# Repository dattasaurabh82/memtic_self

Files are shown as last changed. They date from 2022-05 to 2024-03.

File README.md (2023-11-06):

# memtic_self

* [PROJECT PAGE](https://www.dattasaurabh.com/mi-e-metic-self)
* [INSTALLATION GUIDE](https://dattabaumstudio.notion.site/Mimetic-self-Installation-and-Maintenance-Guide-89d1f03d15b848089516b9a0ae4b9f4f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)

## System Architecture overview:
```mermaid
sequenceDiagram
    autonumber
    participant Processing_GUI
    participant python_AI_API_req_maker
    participant img_data.json
    participant python_gif_req_maker
    participant gif_data.json
    participant PI_python_OMX_player
    participant HW_swiper

    Note over Processing_GUI: mount network loaction of PI
    loop Every few minutes (configurable in app)
        Processing_GUI->>PI_python_OMX_player:  MQTT: stop omx player

        Note over Processing_GUI: capture image
        
        alt got captions and bounding box
            Processing_GUI->>python_AI_API_req_maker: CMD: raw.png + img_data.json

            activate Processing_GUI

            python_AI_API_req_maker-->>img_data.json: FILE_IO: formatted json response
            
            img_data.json-->>Processing_GUI: FILE_IO:parse a random caption and bounding boxes
            
            Processing_GUI->>python_gif_req_maker: CMD: caption + gif_data.json

            activate python_gif_req_maker

            python_gif_req_maker-->>gif_data.json: FILE_IO: formatted json response

            gif_data.json-->>Processing_GUI: FILE_IO: parse gif url

            deactivate python_gif_req_maker

            Note over Processing_GUI: download gif in network location

            Processing_GUI->>PI_python_OMX_player: CURL: MQTT: start omx player 

            deactivate Processing_GUI

            Note over PI_python_OMX_player: loop new GIF
        
        else caption req error
            Processing_GUI-xpython_AI_API_req_maker: CMD: raw.png + img_data.json

            activate Processing_GUI
            
            python_AI_API_req_maker-ximg_data.json: FILE_IO: exception for json response
            
            Processing_GUI->>PI_python_OMX_player: CURL: show error gif + MQTT: start omx player 

            deactivate Processing_GUI

            Note over PI_python_OMX_player: loop error fixed GIF
        else gif req error
            Processing_GUI->>python_AI_API_req_maker: CMD: raw.png + img_data.json

            activate Processing_GUI
            
            python_AI_API_req_maker->>img_data.json: FILE_IO: exception for json response

            img_data.json-->>Processing_GUI: FILE_IO:parse a random caption and bounding boxes
            
            Processing_GUI-xpython_gif_req_maker: CMD: caption + gif_data.json

            python_gif_req_maker--xgif_data.json: FILE_IO: exception for json response

            Processing_GUI->>PI_python_OMX_player: CURL: show error gif + MQTT: start omx player 

            deactivate Processing_GUI

            Note over PI_python_OMX_player: loop error fixed GIF
        end

        Note over Processing_GUI,HW_swiper: In any case, it send a swipe signal and awaits for swipe finish

        Processing_GUI->>HW_swiper: SERIAL: scroll tiktok
        activate Processing_GUI
       
        Note over HW_swiper: Swipe
        
        activate HW_swiper
        
        HW_swiper->>Processing_GUI: done swipping
        deactivate HW_swiper
        deactivate Processing_GUI
    end
    
```

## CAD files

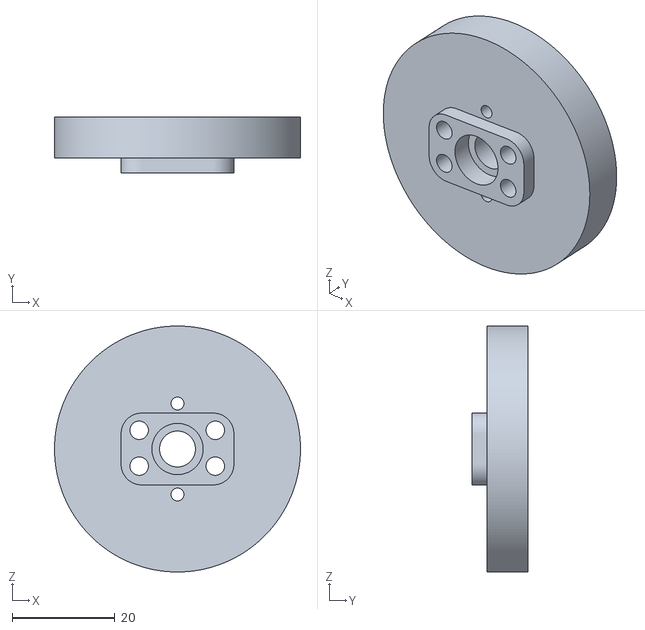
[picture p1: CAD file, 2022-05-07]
3D parts and laser cuts/camSwipper/CameraHolder.stl
48.0 x 11.0 x 48.0

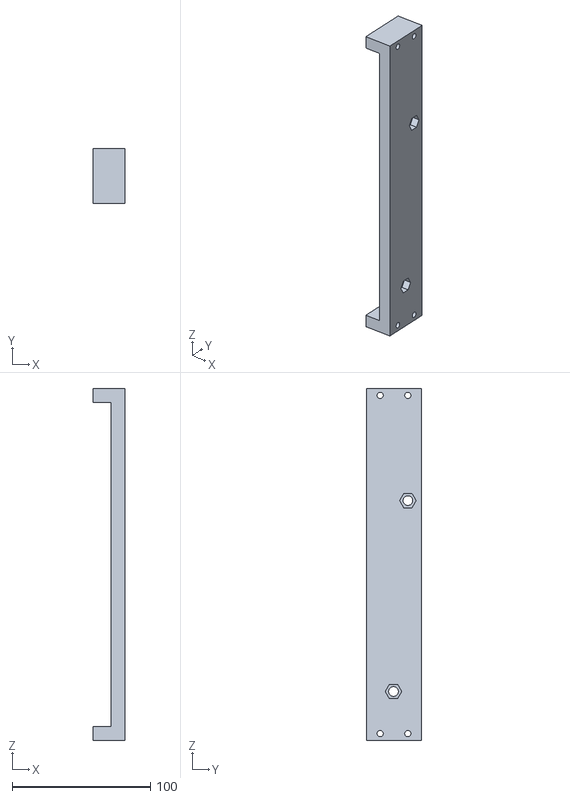
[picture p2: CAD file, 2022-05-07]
3D parts and laser cuts/ScreenHolder.stl
23.2 x 40.0 x 255.0

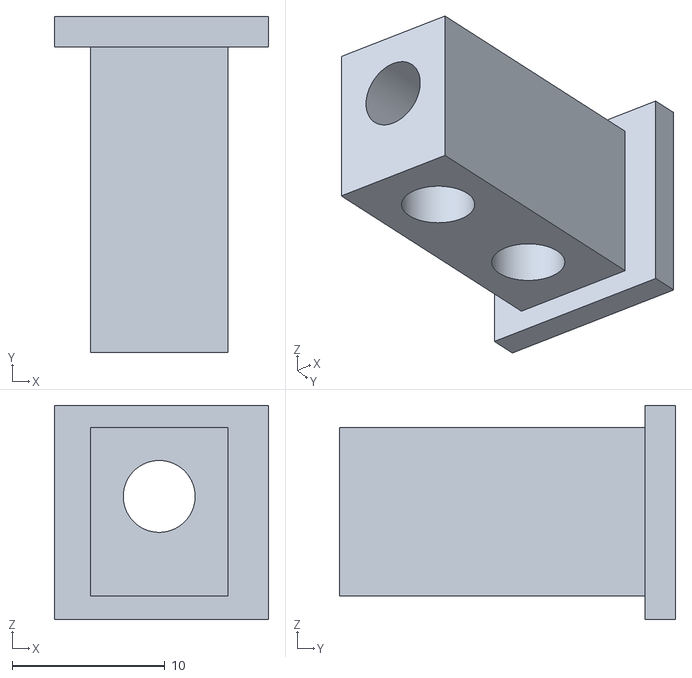
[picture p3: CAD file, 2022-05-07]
3D parts and laser cuts/camSwipper/HolderConnector.stl
14.0 x 22.0 x 14.0

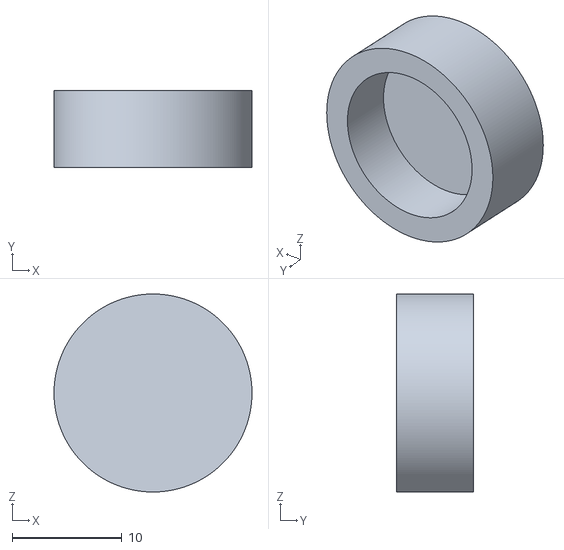
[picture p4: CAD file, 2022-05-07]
3D parts and laser cuts/bearingCover.stl
18.0 x 7.00 x 18.0

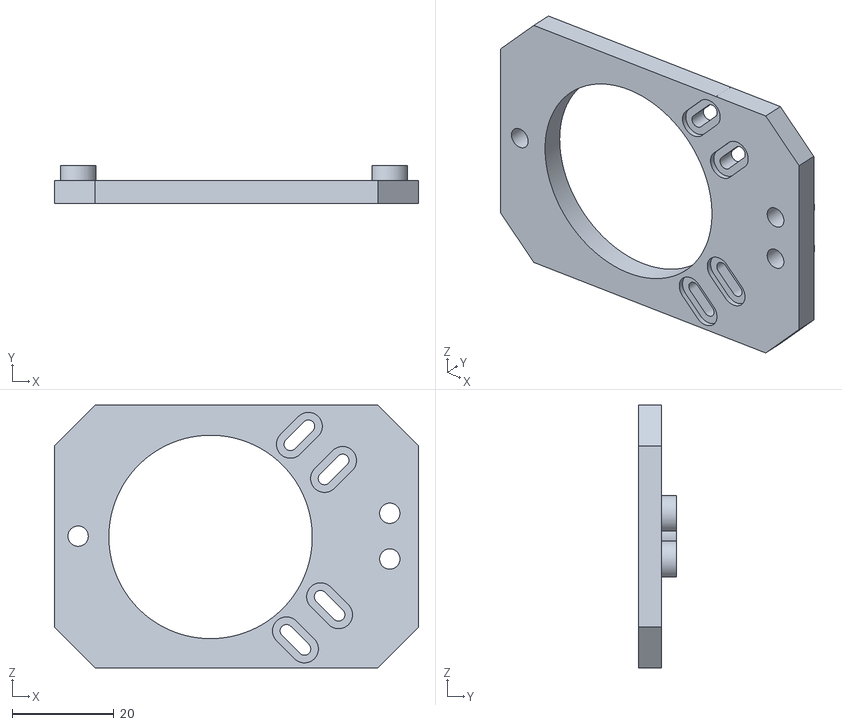
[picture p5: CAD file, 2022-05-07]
3D parts and laser cuts/camSwipper/TopPlateBigHole.stl
71.6 x 7.50 x 51.7

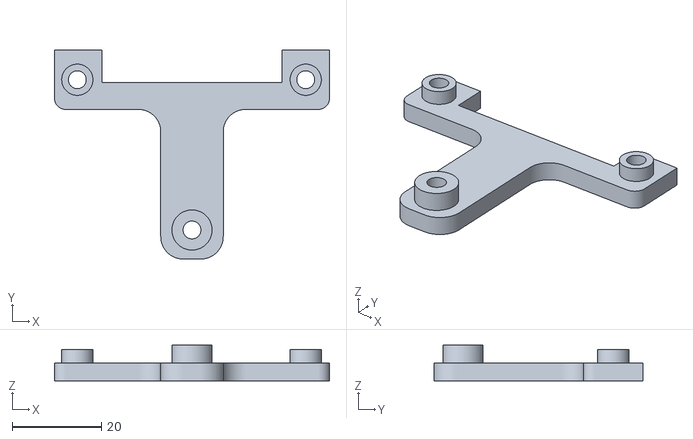
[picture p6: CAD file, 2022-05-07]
3D parts and laser cuts/camSwipper/FrontRightHolder.stl
61.6 x 46.8 x 8.00

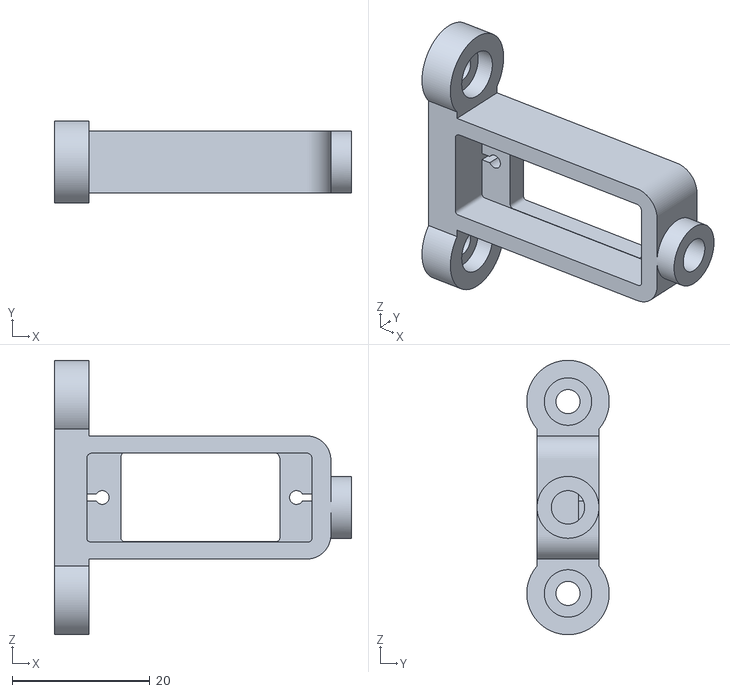
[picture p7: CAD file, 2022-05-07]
3D parts and laser cuts/ServoMount.stl
43.2 x 12.0 x 39.9

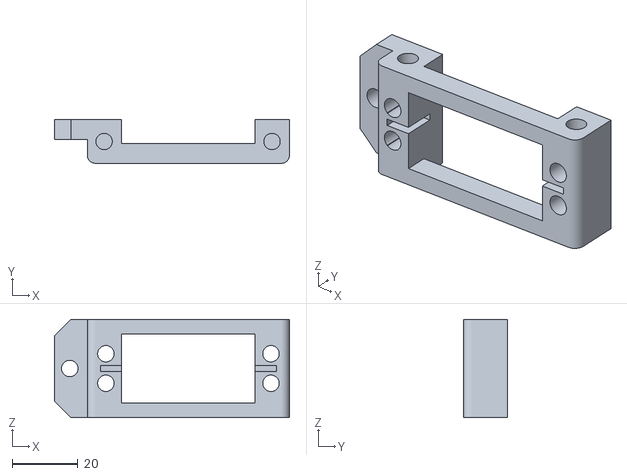
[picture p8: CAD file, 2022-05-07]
3D parts and laser cuts/camSwipper/ServoHolder.stl
71.6 x 13.3 x 30.0

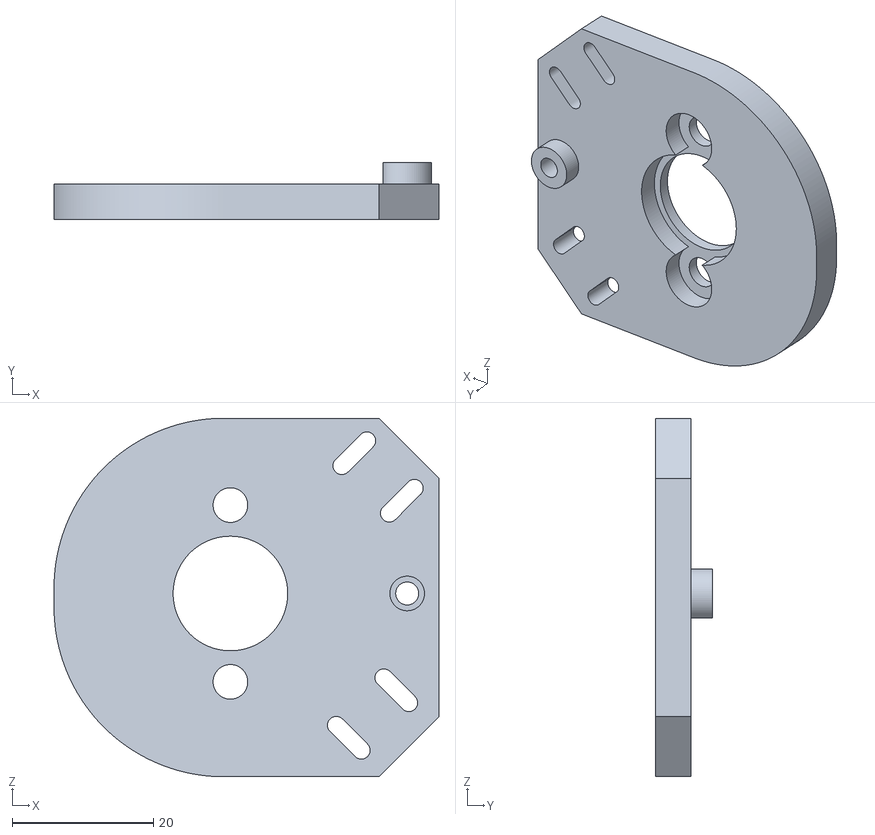
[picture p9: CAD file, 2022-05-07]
3D parts and laser cuts/TopPlate.stl
54.5 x 8.00 x 50.7

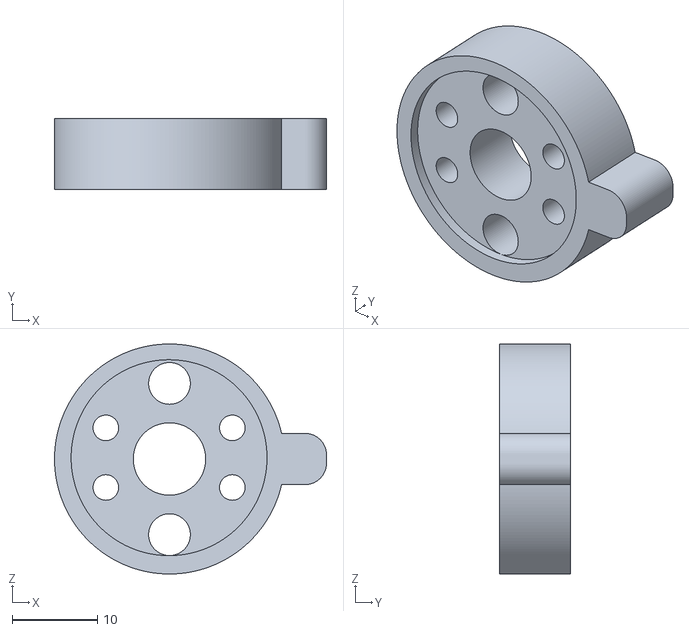
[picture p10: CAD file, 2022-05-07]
3D parts and laser cuts/camSwipper/limiter.stl
31.9 x 8.30 x 27.0

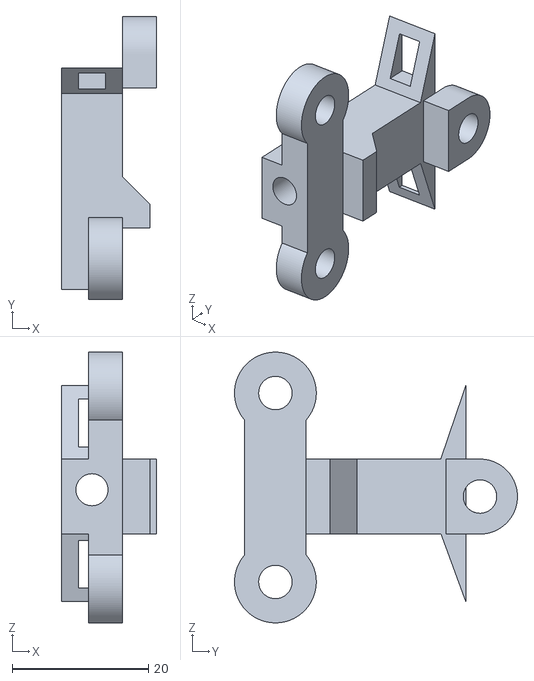
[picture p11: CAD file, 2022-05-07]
3D parts and laser cuts/RodHolder.stl
14.0 x 41.5 x 39.7

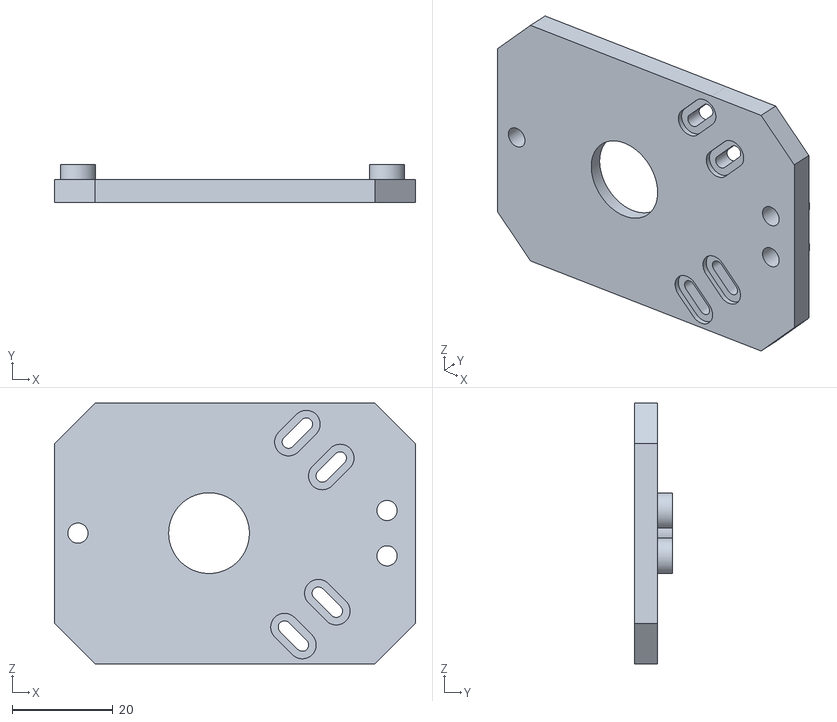
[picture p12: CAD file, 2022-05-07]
3D parts and laser cuts/camSwipper/TopPlate.stl
71.6 x 7.50 x 51.7

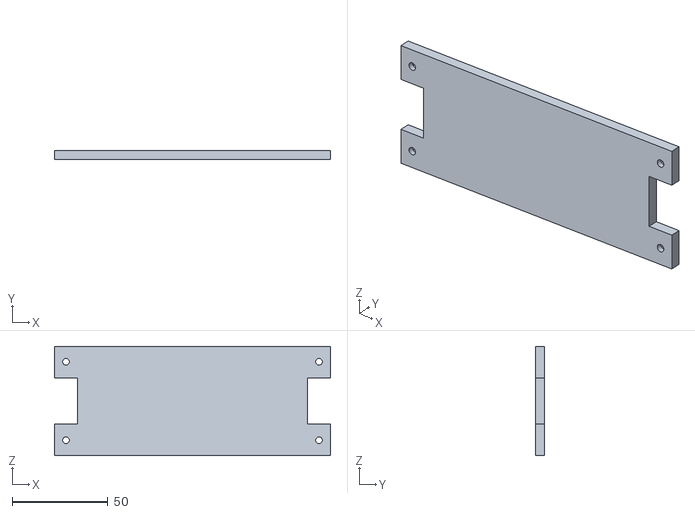
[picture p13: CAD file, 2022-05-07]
3D parts and laser cuts/topBack.stl
144.2 x 4.90 x 57.0

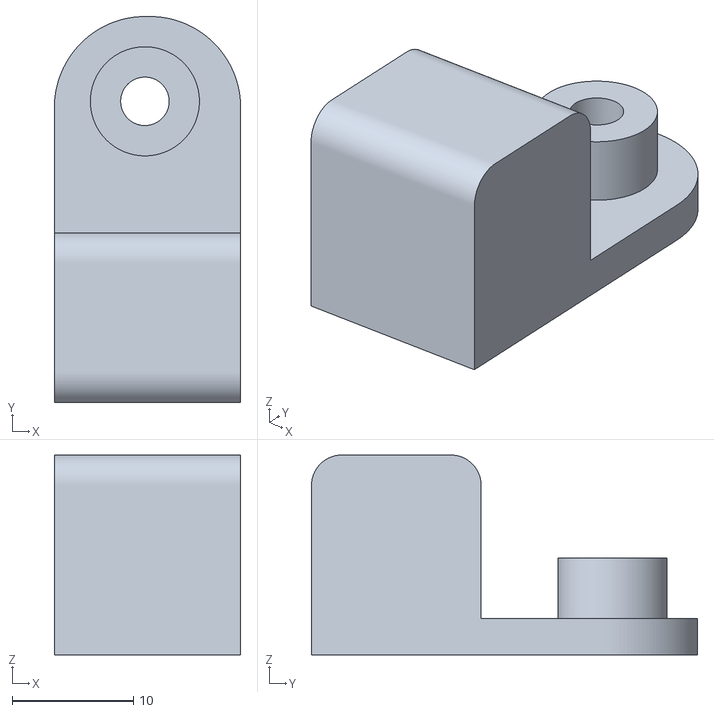
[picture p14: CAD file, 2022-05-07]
3D parts and laser cuts/camSwipper/TRRS Holder.stl
15.4 x 31.9 x 16.5

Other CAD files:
3D parts and laser cuts/bottomBack.stl
3D parts and laser cuts/camSwipper/BottomBracket.stl
3D parts and laser cuts/camSwipper/BackLeftHolder.stl
3D parts and laser cuts/Power boards holder.stl
3D parts and laser cuts/2662N390_PLASTIC GEAR - 20 DEGREE PRESSURE ANGLE.stl
3D parts and laser cuts/2664N544_METAL GEAR - 20 DEGREE PRESSURE ANGLE.stl
3D parts and laser cuts/Angle Connector.stl
3D parts and laser cuts/GlueLayer.dxf
3D parts and laser cuts/HolderConnector.stl
3D parts and laser cuts/HolderConnectorV3.stl
3D parts and laser cuts/NUC POwer supply holder.stl
3D parts and laser cuts/PlexiLayer.dxf
3D parts and laser cuts/ScrewBearingHolder.stl
3D parts and laser cuts/ScrewBearingHolderThinner.stl
3D parts and laser cuts/ScrewBearingPusherSurface.stl
3D parts and laser cuts/ServoMountSecure.stl
3D parts and laser cuts/TRRS Holder.stl
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

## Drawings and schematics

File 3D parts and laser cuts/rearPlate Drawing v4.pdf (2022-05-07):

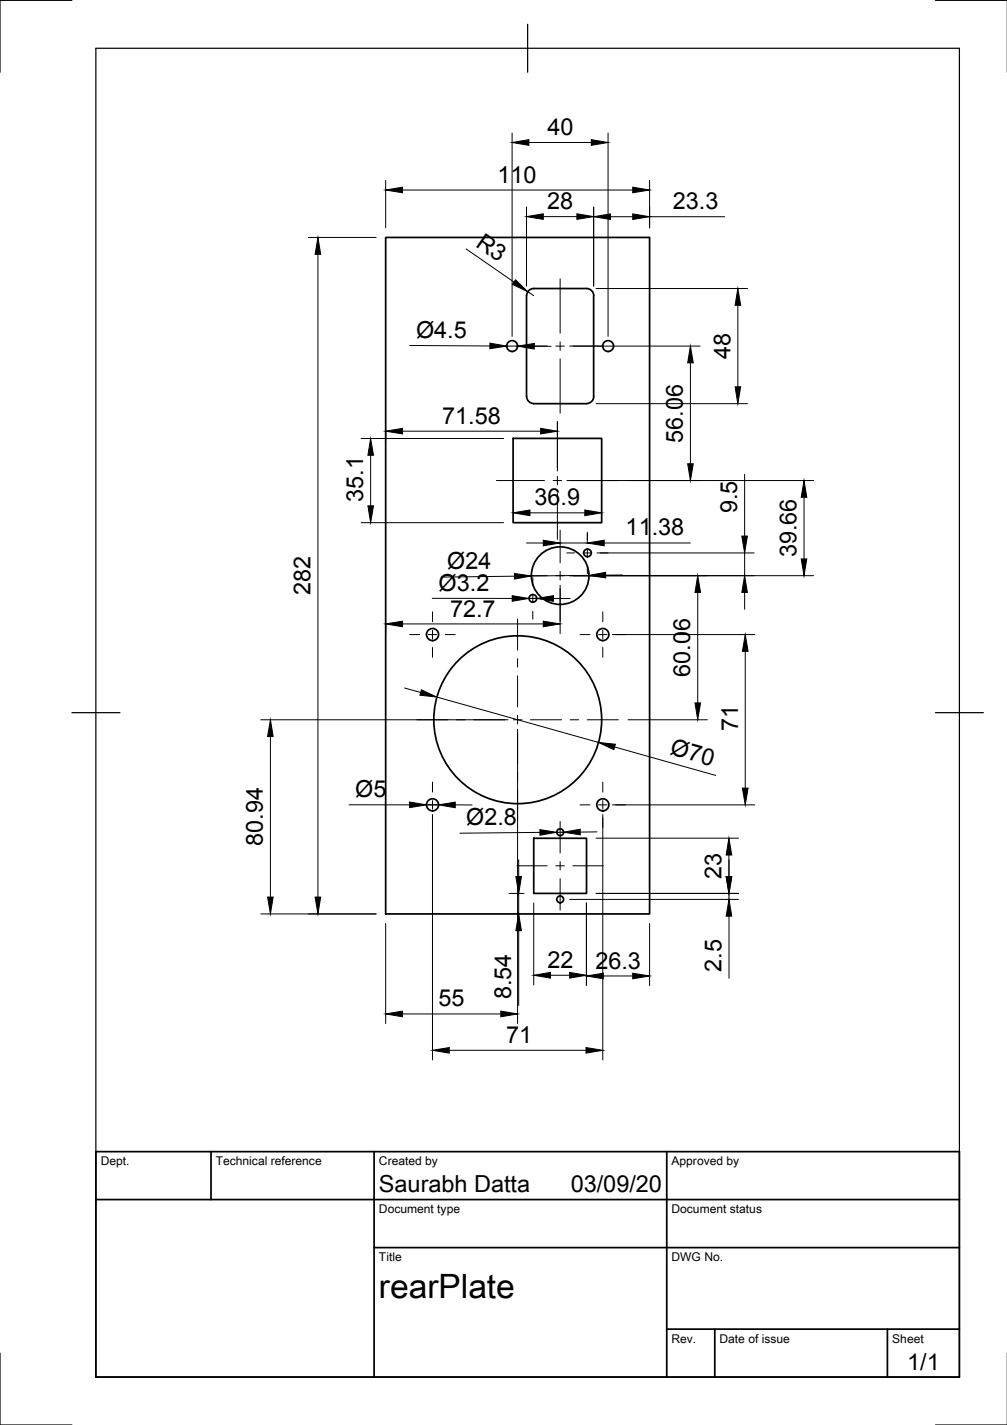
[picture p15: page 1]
Saurabh Datta 282

Dept. | Technical reference | Created by 03/09/20 | Approved by

Document type | Document status

Title rearPlate | DWG No.

Rev. | Date of issue | Sheet 1/1

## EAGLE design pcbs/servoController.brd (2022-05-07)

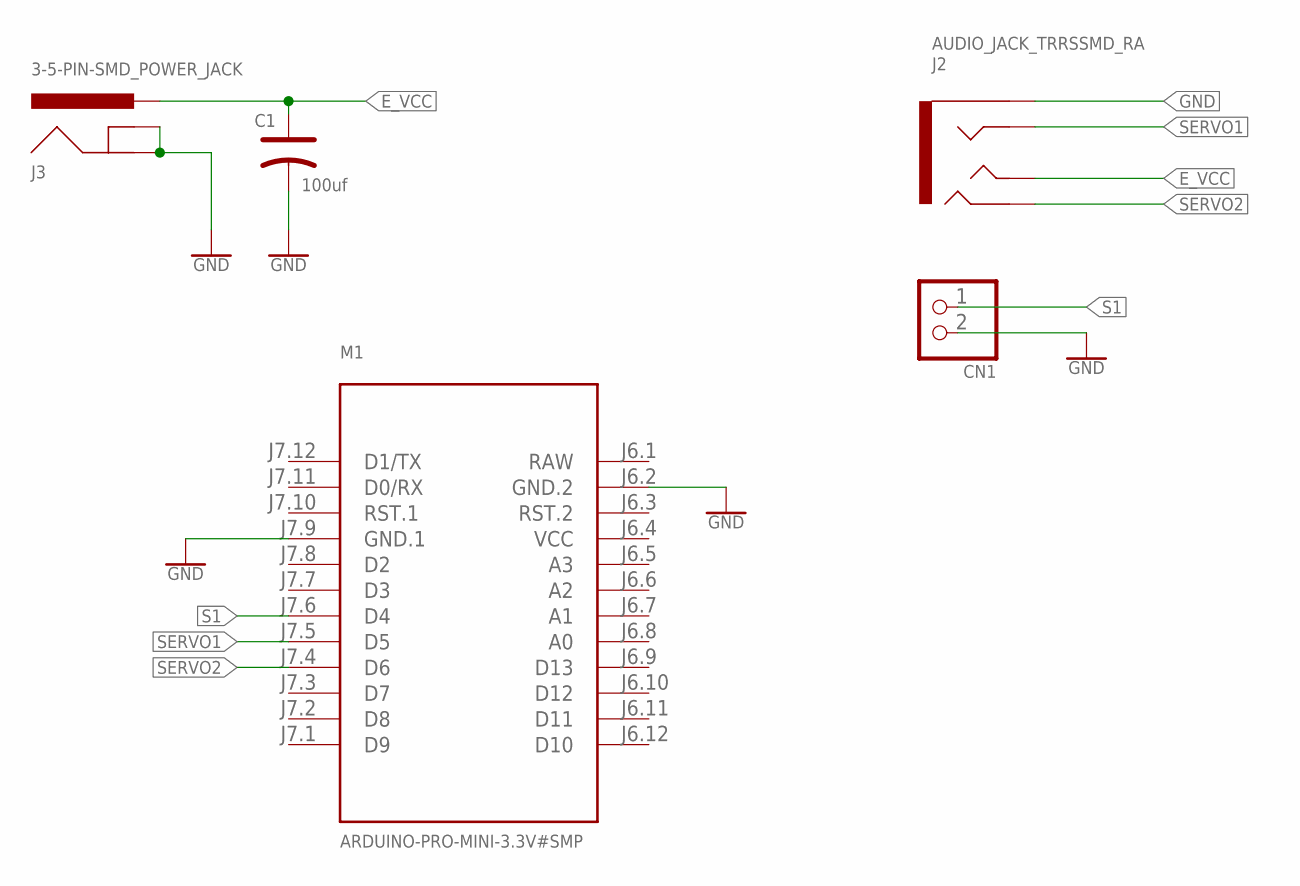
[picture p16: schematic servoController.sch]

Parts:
C1: 100uf; PC-D5.3MM
CN1: ARDUINO_3V_TTL_INTERFACE_2_PI_ADAFRUIT_JST_2PIN-S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; ARDUINO_3V_TTL_INTERFACE_2_PI_ADAFRUIT_JST-PH-2-SMT-RA
J2: AUDIO_JACK_TRRSSMD_RA; AUDIO_JACK_3.5MM_TRRS_SMD_RA
J3: 3-5-PIN-SMD_POWER_JACK; 3-5-PIN-SMD_POWER_JACK_PTH
M1: ARDUINO-PRO-MINI-3.3V#SMP; ARDUINO-PRO-MINI#SMP

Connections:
E_VCC: C1.+, J2.TIP, J3.PWR
GND: C1.-, CN1.2 (1), J2.EARTH, J3.GND, J3.GNDBREAK, M1.J6.2 (GND.2), M1.J7.9 (GND.1)
RAW: M1.J6.1 (RAW)
S1: CN1.1 (2), M1.J7.6 (D4)
SERVO1: J2.RING1, M1.J7.5 (D5)
SERVO2: J2.RING2, M1.J7.4 (D6)
VCC: M1.J6.4 (VCC)

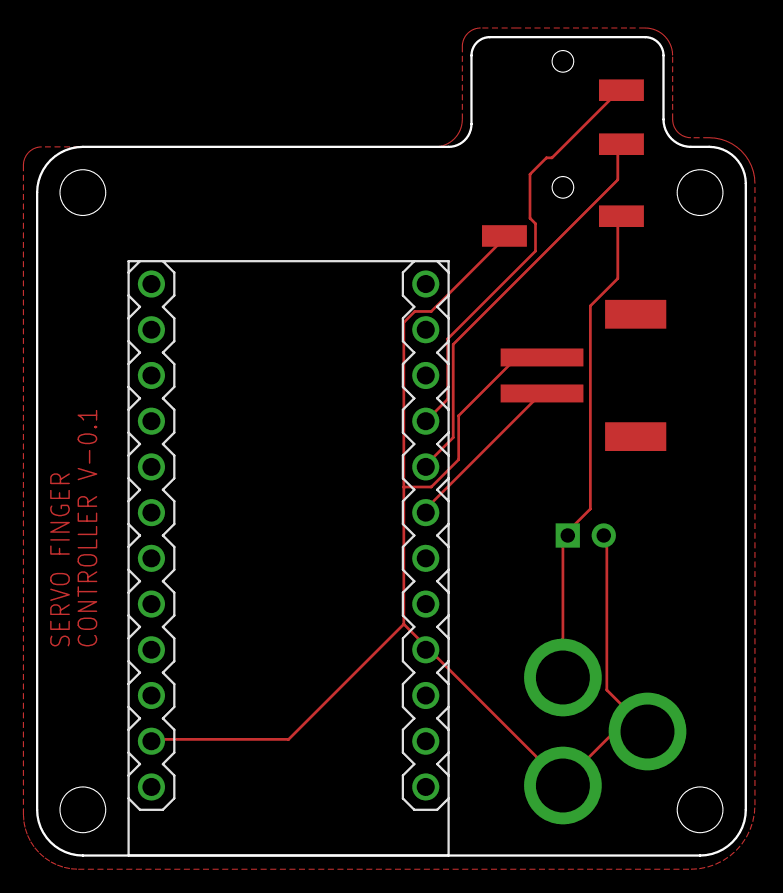
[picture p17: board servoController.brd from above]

Board: 2 copper layers, 39.4 x 45.5 mm, 5 parts (0 on the bottom side), 5 nets.

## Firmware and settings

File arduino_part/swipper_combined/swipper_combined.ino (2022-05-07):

const int motorSigPin = 5;

#include <AceButton.h>
using namespace ace_button;

const uint8_t NUM_BTNS = 3;

const int BUTTON_PIN = 4;
const int LIMIT_BUTTON_PIN = 6;
const int ARMING_BUTTON_PIN = 7;
const int RXLED = 17;


struct Info {
  const uint8_t buttonPin;
};

Info INFOS[NUM_BTNS] = {
  {BUTTON_PIN},
  {LIMIT_BUTTON_PIN},
  {ARMING_BUTTON_PIN}
};

AceButton buttons[NUM_BTNS];

void handleEvent(AceButton*, uint8_t, uint8_t);

char value;

boolean sysNotArmed;
boolean doSwipe;
boolean swipeComplete;
boolean sendSig = false;

#include <Servo.h>
Servo camServo;

boolean doCamSwipe;
boolean camLimitsHit;


#include <AsyncDelay.h>

AsyncDelay delay_s;

const int nextProcessStartDelayForProcessing = 3000; // 3 sec



void setup() {
  Serial.begin(115200);

  pinMode(RXLED , OUTPUT);
  digitalWrite(RXLED , LOW);

  for (uint8_t i = 0; i < NUM_BTNS; i++) {
    pinMode(INFOS[i].buttonPin, INPUT_PULLUP);
    buttons[i].init(INFOS[i].buttonPin, HIGH, i);
  }

  ButtonConfig* buttonConfig = ButtonConfig::getSystemButtonConfig();
  buttonConfig->setEventHandler(handleEvent);
  buttonConfig->setFeature(ButtonConfig::kFeatureClick);
  buttonConfig->setFeature(ButtonConfig::kFeatureLongPress);

  //  pinMode(motorSigPin, OUTPUT);
  //  digitalWrite(motorSigPin, LOW);
}


int sketchNum = 1;
bool pinTypeAssigned = false;
bool swipeLeft, swipeRight;
int dirSelector = 0;

void loop() {
  for (uint8_t i = 0; i < NUM_BTNS; i++) {
    buttons[i].check();
  }

  if (Serial.available()) {
    value = Serial.read();

    if (value == '2' /* processing sketch 1 for tik-tok */) {
      sketchNum = 1;

      pinTypeAssigned = false;

      if (!pinTypeAssigned) {
        pinMode(motorSigPin, OUTPUT);
        digitalWrite(motorSigPin, LOW);
        pinTypeAssigned = true;
      }
    }

    if (value == '3' /* processing sketch 2 for env watch */) {
      sketchNum = 2;

      pinTypeAssigned = false;

      if (!pinTypeAssigned) {
        camServo.attach(motorSigPin);
        pinTypeAssigned = true;
      }
    }

    if (value == '1') {     /* if it receives signal to do a swipe */
      if (sketchNum == 1) { /* if it is processing sketch 1 for tik-tok */
        if (!doSwipe) {
          doSwipe = true;
          doCamSwipe = false;
          swipeComplete = false;
        }
      }
      if (sketchNum == 2) { /* if it is processing sketch 2 for env watch */
        if (!doCamSwipe) {
          doCamSwipe = true;
          doSwipe = false;
          camLimitsHit = false;
        }
      }
    }
  }

  //-------------------------------------------//
  //----------- Tik-Tok Swipper Part ----------//
  //-------------------------------------------//
  if (sketchNum == 1) {
    if (doSwipe) {
      if (!swipeComplete) digitalWrite(motorSigPin, HIGH);
      doSwipe = false;
    }


    if (swipeComplete) {
      delay(100); // play with this value here
      digitalWrite(motorSigPin, LOW);

      delay_s.start(nextProcessStartDelayForProcessing, AsyncDelay::MILLIS);

      sendSig = true;
      swipeComplete = false;
    }
  }
  //------------------------*******************************************-------------------//


  //-------------------------------------------//
  //------ Env Scanning Cam Swipper Part ------//
  //-------------------------------------------//
  if (sketchNum == 2) {
    if (doCamSwipe) {
      // pick randomly left or right
      dirSelector = int(random(2));
      if (dirSelector == 0) {
        swipeLeft = true;
        swipeRight = false;
      }
      if (dirSelector == 1) {
        swipeLeft = false;
        swipeRight = true;
      }

      if (swipeLeft) {
        // Set motion in one direction
        if (!camLimitsHit) camServo.write(81);
      }
      if (swipeRight)
        // Set motion in another direction
        if (!camLimitsHit) camServo.write(99);
    }
    doCamSwipe = false;
  }

  if (camLimitsHit) {
    // stop immediately
    camServo.write(90);
    // and after a certain delay
    delay(100);
    // reverse the direction
    // if it was going left, then now go right
    if (swipeLeft) camServo.write(99);
    // if it was going right, then now go left
    if (swipeRight) camServo.write(81);

    // after a random delay
    /*-- WORK ON THE RANGE HERE --*/
    delay(int(random(300, 600)));
    // Stop the motor
    camServo.write(90);

    // start the delay to send sig to processing
    delay_s.start(nextProcessStartDelayForProcessing, AsyncDelay::MILLIS);

    sendSig = true;
    camLimitsHit = false;
  }


  //------------------------*******************************************-------------------//


  if (delay_s.isExpired() && sendSig) {
    Serial.println("s");
    sendSig = false;
  }

}



void handleEvent(AceButton* button, uint8_t eventType, uint8_t buttonState) {
  uint8_t id = button->getId();
  uint8_t buttonPin = INFOS[id].buttonPin;

  switch (eventType) {
    case AceButton::kEventLongPressed:
      if (buttonPin == BUTTON_PIN) {
        if (sketchNum == 1) {
          doSwipe = true;
          swipeComplete = false;
        }
        if (sketchNum == 2) {
          doCamSwipe = true;
          camLimitsHit = true;
        }
      }
      if (buttonPin == LIMIT_BUTTON_PIN) {
        if (sketchNum == 1) swipeComplete = true;
        if (sketchNum == 2) camLimitsHit = true;
      }
      if (buttonPin == ARMING_BUTTON_PIN) {
        sysNotArmed = !sysNotArmed;
        if (sysNotArmed) {
          Serial.println("e");
          digitalWrite(RXLED , HIGH);
        } else {
          Serial.println("d");
          digitalWrite(RXLED , LOW);
        }
      }
    case AceButton::kEventPressed:
      if (buttonPin == BUTTON_PIN) {
        if (sketchNum == 1) {
          doSwipe = true;
          swipeComplete = false;
        }
        if (sketchNum == 2) {
          doCamSwipe = true;
          camLimitsHit = true;
        }
      }
      if (buttonPin == LIMIT_BUTTON_PIN) {
        if (sketchNum == 1) swipeComplete = true;
        if (sketchNum == 2) camLimitsHit = true;
      }
      if (buttonPin == ARMING_BUTTON_PIN) {
        sysNotArmed = !sysNotArmed;
        if (sysNotArmed) {
          Serial.println("e");
          digitalWrite(RXLED , HIGH);
        } else {
          Serial.println("d");
          digitalWrite(RXLED , LOW);
        }
      }
      break;
  }
}

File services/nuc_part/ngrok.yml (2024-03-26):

version: "2"
authtoken: 
region: jp
tunnels:
  ssh:
    addr: 22
    proto: tcp
    remote_addr: 1.tcp.jp.ngrok.io:24291
  vnc:
    addr: 5900
    proto: tcp
    remote_addr: 1.tcp.jp.ngrok.io:24591
